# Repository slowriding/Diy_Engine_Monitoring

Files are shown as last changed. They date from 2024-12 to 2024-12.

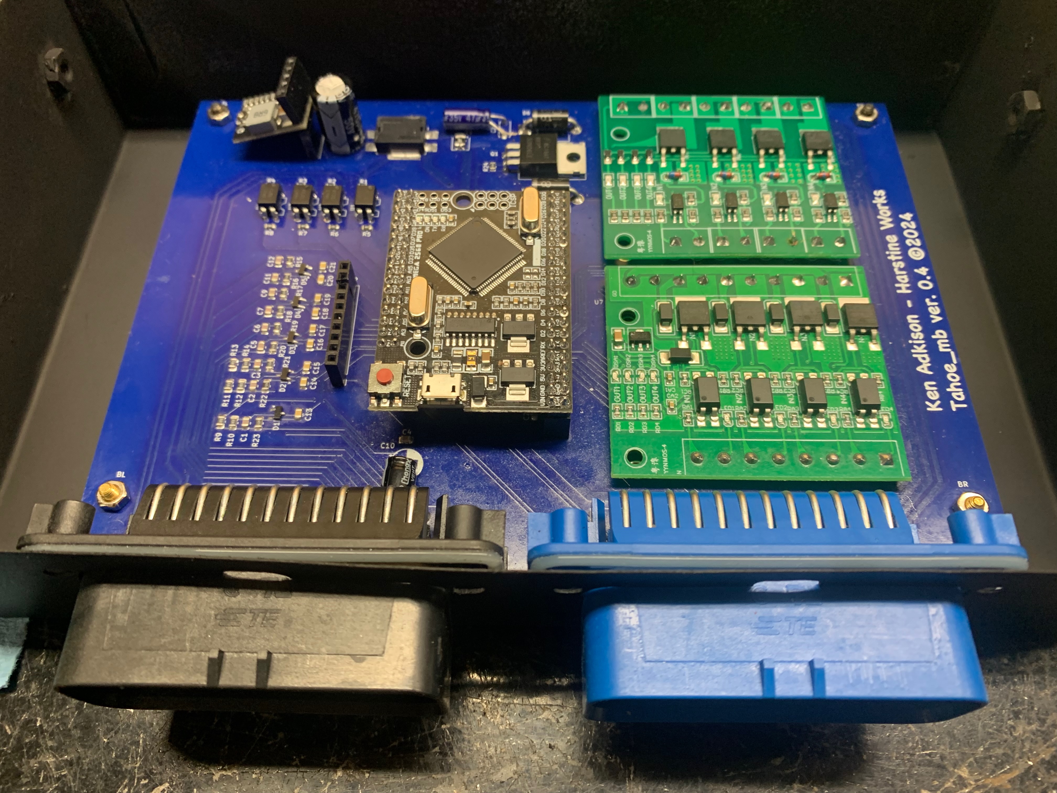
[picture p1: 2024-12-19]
PCB.jpeg

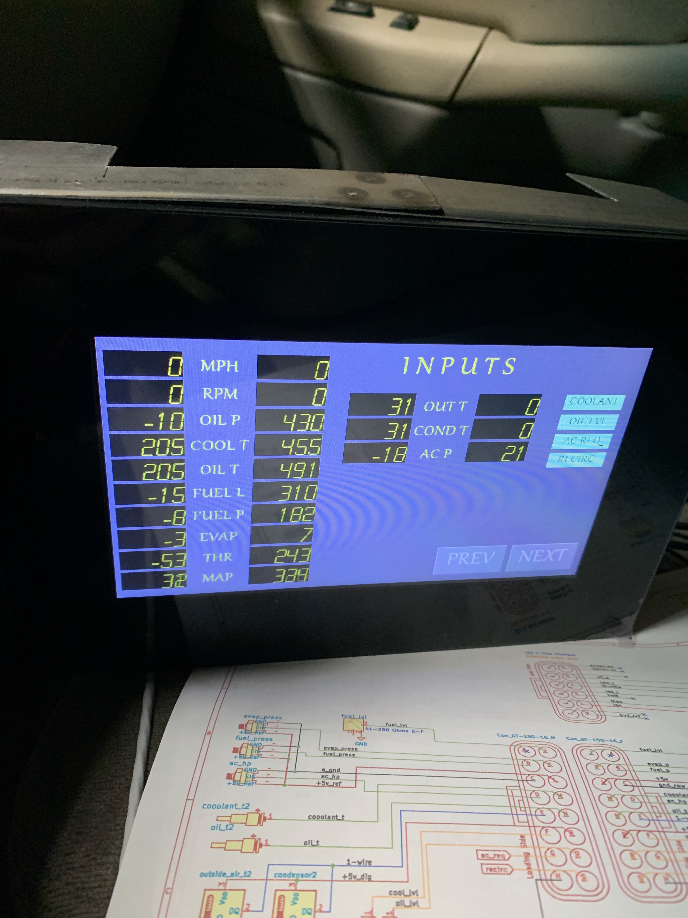
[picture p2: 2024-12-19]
Early_screenshot.jpeg

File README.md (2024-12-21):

# Diy_Engine_Monitoring
Read and display Powertrain sensors and control outputs with DIY PCB, code and display.

Project started to facilitate features lost due to swapping in newer engine into older computer controlled vehicle.
It overlays a secondary set of sensors and display unit showing gauges.
The controller drive outputs for variable speed loads like fans and fuel pump and switched loads.
Goals are for the system to be as simple as possible, hackable and start immediately without having to boot an operating system.

Project started to facilitate features lost due to swapping in newer engine into older computer controlled vehicle.
It overlays a secondary set of sensors and a display unit showing gauges.
The controller drives outputs for variable speed loads like fans and fuel pump and switched loads.
Goals are for the system to be as simple as possible, hackable and start immediately without having to boot an operating system.

Current design uses a common Arduino module programmed in C.  This project welcomes submissions of improvements or complete redesigns.
OBDII and GM LAN integration are intended but not completed.

Test article implementation:
2002 Chevrolet Tahoe with 5.3L gas engine failed and Chevrolet Performance E-ROD LS3 powertrain was installed with 6-speed manual transmission necessitating ECU swap.
The communications network is too different to interconnect directly.
The original dashboard gauges and A/C became completely non-functional due to the communications bus changes and features not implemented in newer but generic engine controller.

This project side steps difficulties in attempting to build a protocol converter; for the time being.
Requirements are met by adding a layer of sensors and outputs to replace missing features and adding some extra functionality.
I (original contributor) intend to hack my 2002 Tahoe dash to driving of stock gauge needles.
This will also control new style variable A/C compressor based on pressure and temperature sensors.

Design overview:
Sensors types:  // currently implemented but not all yet working.
	Resistive (coolant & oil temp and fuel level).
	0-5V transducers (oil, fuel, evap. and A/C high pressure)
	0-5V ECU outputs (throttle and map)
	Pulse frequency (RPM and vehicle speed ~10-14V)
	Switched (ac & recirculation requests)
	1-wire temperature probes (outside air and A/C condenser temperatures)

Outputs types:
	PWM Gauges Drivers (fuel level, oil pressure, coolant temperature, MPH)
	PWM Loads (fan1, fan2, Variable A/C compressor, Fuel Pump speed)

Interface:
	Display - Nextion brand Intelligent LCD display used due to it’s simple serial port/text based connection.
	All the graphics are stored and processed on the display.
	I2c & SPI connections for future ODB2 interfaces.

Programming:
	Currently written in C with migration to RUST intended for future releases.
	The Tahoe.h file isolates MCU pin definitions, calibrations and variable definitions.

Files:
	Schmatic: See .pdf files in root or Open directorys in KiCAD One is the PCB and the other shows the wiring currenly used on authors Tahoe

Code: Open Using Arduino software

Please consider contributing to this evolving project as much can be improved

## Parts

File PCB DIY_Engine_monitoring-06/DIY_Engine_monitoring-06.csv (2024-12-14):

Source: | /Users/kennethadkison/syncthing/tahoe/KiCAD/Tahoe_inputs_PCB-0_4/Tahoe_inputs_PCB-0_4.kicad_sch
Date: | Wednesday, December 06, 2023 at 08:47:50 AM
Tool: | Eeschema 7.0.9
Generator: | /Applications/KiCad/KiCad.app/Contents/SharedSupport/plugins/bom_csv_grouped_by_value_with_fp.py
Component Count: | 74
Ref | Qnty | Value | Cmp name | Footprint | Description | Vendor | DNP
C1, C2, C3, C4, C5, C6, C7, C8, C9, C10, C11, C12 | 12 | .1uf | C_Small | Capacitor_SMD:C_0805_2012Metric_Pad1.18x1.45mm_HandSolder | Unpolarized capacitor, small symbol
C13, C14 | 2 | 47uf_35v | C_Polarized_Small | Capacitor_THT:CP_Radial_D6.3mm_P2.50mm | Polarized capacitor, small symbol
C15, C16, C17, C18, C19, C20, C21, C22, C23, C24, C25, C26 | 12 | .22uf | C_Small | Capacitor_SMD:C_0805_2012Metric_Pad1.18x1.45mm_HandSolder | Unpolarized capacitor, small symbol
C27, C28, C29 | 3 | 100nf | C_Small | Capacitor_SMD:C_0805_2012Metric_Pad1.18x1.45mm_HandSolder | Unpolarized capacitor, small symbol
C30 | 1 | 1uf | C_Small | Capacitor_SMD:C_0805_2012Metric_Pad1.18x1.45mm_HandSolder | Unpolarized capacitor, small symbol
C31, C32 | 2 | 0.1uf | C_Small | Capacitor_SMD:C_0805_2012Metric_Pad1.18x1.45mm_HandSolder | Unpolarized capacitor, small symbol
D1, D2, D3, D4, D5, D6 | 6 | BZB84-B5V1,215 | BZB84-B5V1,215_2 | Package_TO_SOT_SMD:SOT-23-3 | 300mW Double Zener Diode, SOT-23
F1 | 1 | Polyfuse_0.5A | Polyfuse_Small | Diode_SMD:Littelfuse_PolyZen-LS | Resettable fuse, polymeric positive temperature coefficient, small symbol
FL1 | 1 | BNX025H01L | Filter_BNX025H01L | BNX025H01L:FIL_BNX025H01L
J1 | 1 | 5V_P/S | Conn_01x05 | Connector_PinHeader_2.54mm:PinHeader_1x05_P2.54mm_Vertical | Generic connector, single row, 01x05, script generated (kicad-library-utils/schlib/autogen/connector/)
J2 | 1 | Freematics-I2C | Conn_01x04 | Connector_PinHeader_2.54mm:PinHeader_1x04_P2.54mm_Vertical | Generic connector, single row, 01x04, script generated (kicad-library-utils/schlib/autogen/connector/)
J3 | 1 | Screw_Terminal_01x08 | Screw_Terminal_01x08 | Connector_Phoenix_MC_HighVoltage:PhoenixContact_MC_1,5_8-GF-5.08_1x08_P5.08mm_Horizontal_ThreadedFlange_MountHole | Generic screw terminal, single row, 01x08, script generated (kicad-library-utils/schlib/autogen/connector/)
J4, J5 | 2 | Conn_01x08 | Conn_01x08 | Connector_JST:JST_XH_B8B-XH-A_1x08_P2.50mm_Vertical | Generic connector, single row, 01x08, script generated (kicad-library-utils/schlib/autogen/connector/)
J6, J7 | 2 | test_acess | Conn_01x06 | Connector_PinHeader_2.54mm:PinHeader_1x06_P2.54mm_Vertical | Generic connector, single row, 01x06, script generated (kicad-library-utils/schlib/autogen/connector/)
J8 | 1 | 3.3v_P/S | Conn_01x05 | Connector_PinHeader_2.54mm:PinHeader_1x05_P2.54mm_Vertical | Generic connector, single row, 01x05, script generated (kicad-library-utils/schlib/autogen/connector/)
J9 | 1 | CANBus-Dual | Conn_02x09_Odd_Even | Connector_PinHeader_2.54mm:PinHeader_2x09_P2.54mm_Vertical | Generic connector, double row, 02x09, odd/even pin numbering scheme (row 1 odd numbers, row 2 even numbers), script generated (kicad-library-utils/schlib/autogen/connector/)
J10, J11 | 2 | Processor_01x10 | Conn_01x10 | Connector_JST:JST_XH_B10B-XH-A_1x10_P2.50mm_Vertical | Generic connector, single row, 01x10, script generated (kicad-library-utils/schlib/autogen/connector/)
R1, R2, R9, R10 | 4 | 2.49k | R_Small_US | Resistor_SMD:R_1206_3216Metric_Pad1.30x1.75mm_HandSolder | Resistor, small US symbol
R3 | 1 | 470 | R_Small_US | Resistor_SMD:R_1206_3216Metric_Pad1.30x1.75mm_HandSolder | Resistor, small US symbol
R4, R5, R6, R7, R8, R11, R12, R13, R14, R15, R16 | 11 | 470 | R_Small_US | Inductor_SMD:L_1206_3216Metric_Pad1.42x1.75mm_HandSolder | Resistor, small US symbol
R17, R18 | 2 | 10kΩ | R | Inductor_SMD:L_1206_3216Metric_Pad1.22x1.90mm_HandSolder | Resistor
SW1 | 1 | PWR_Source | SW_SPDT | Button_Switch_SMD:SW_SPDT_PCM12 | Switch, single pole double throw
U1, U2, U3 | 3 | ADS1115IDGS | ADS1115IDGS | Package_SO:TSSOP-10_3x3mm_P0.5mm | Ultra-Small, Low-Power, I2C-Compatible, 860-SPS, 16-Bit ADCs With Internal Reference, Oscillator, and Programmable Comparator, VSSOP-10
U4 | 1 | TXS0108EPW | TXS0108EPW | Package_SO:TSSOP-20_4.4x6.5mm_P0.65mm | Bidirectional level-shifting voltage translator, TSSOP-20

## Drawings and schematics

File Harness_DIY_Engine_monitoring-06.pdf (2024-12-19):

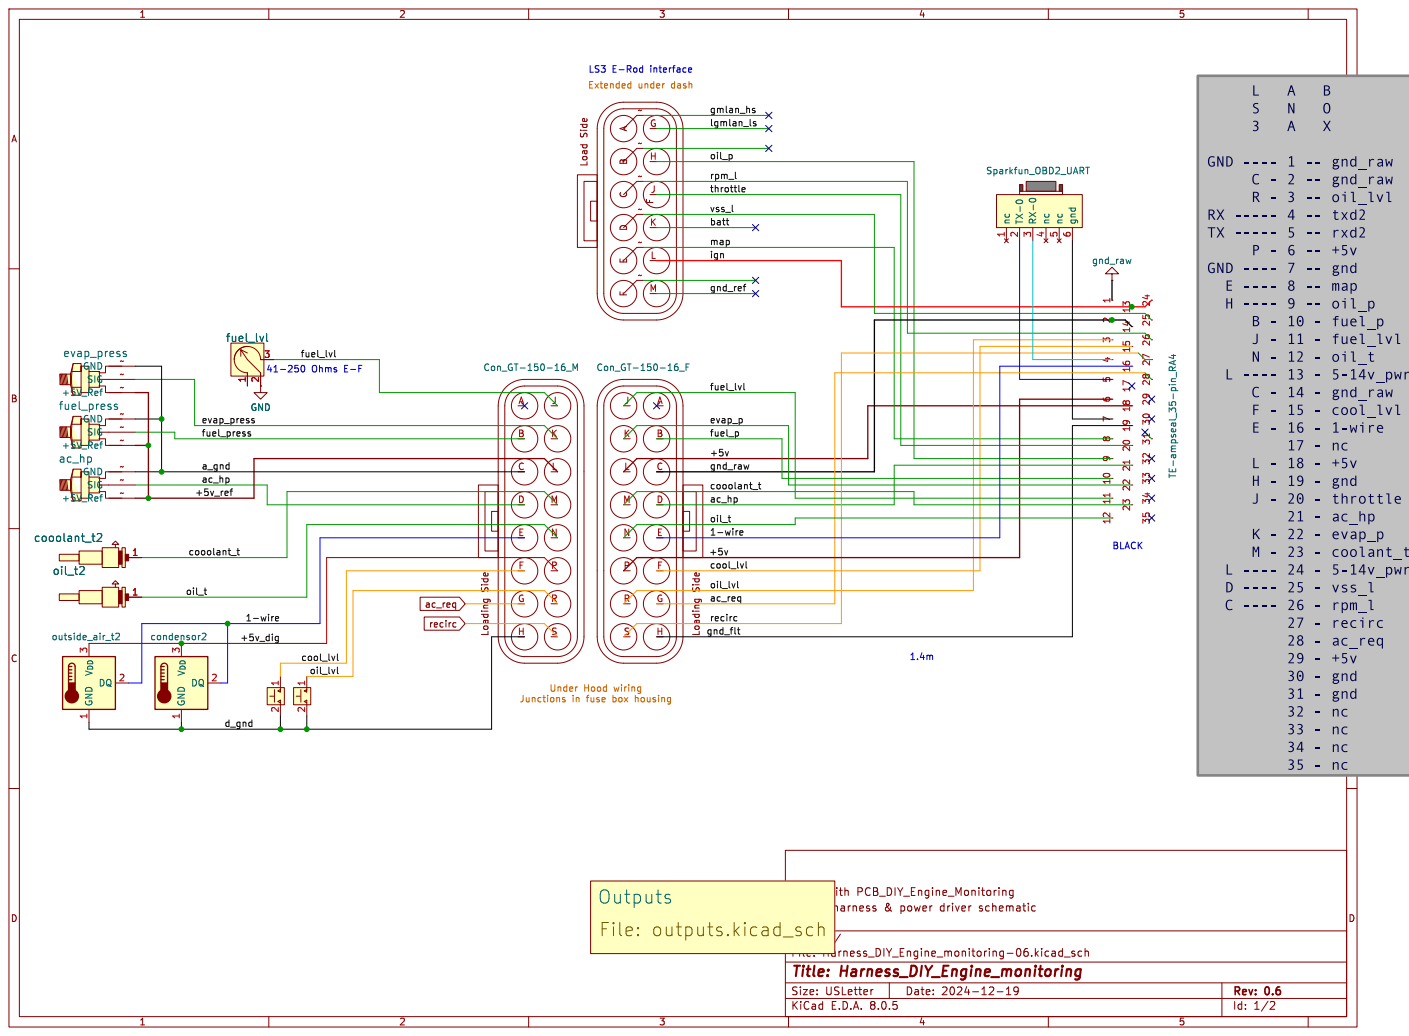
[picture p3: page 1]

1 2 http://docs.longan-labs.cc/1030019/ VIN

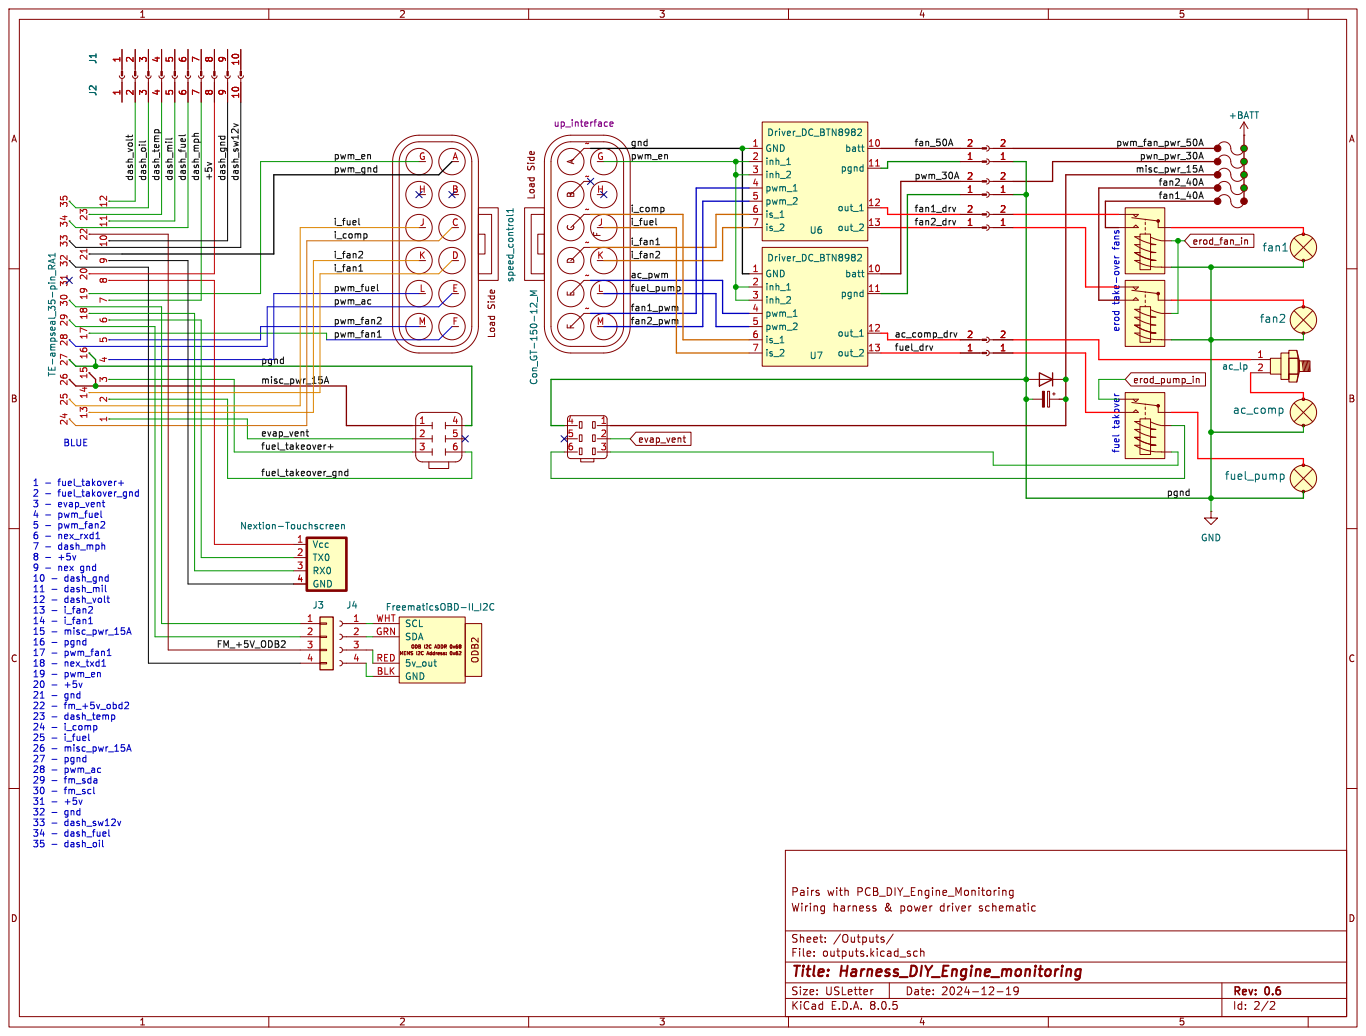
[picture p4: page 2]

+BATT
pwm_fan_pwr_50A erod take-over fans fuel takover

Wiring harness & | | PCB_DIY_Engine_Monitoring | power | driver schematic Pairs with

E.D.A. 8.0.5 Size: USLetter | Rev: 0.6 | | | | D Date: 2024-12-19 KiCad

File: outputs.kicad_sch Sheet: /Outputs/
Id: 2/2 Title: Harness_DIY_Engine_monitoring

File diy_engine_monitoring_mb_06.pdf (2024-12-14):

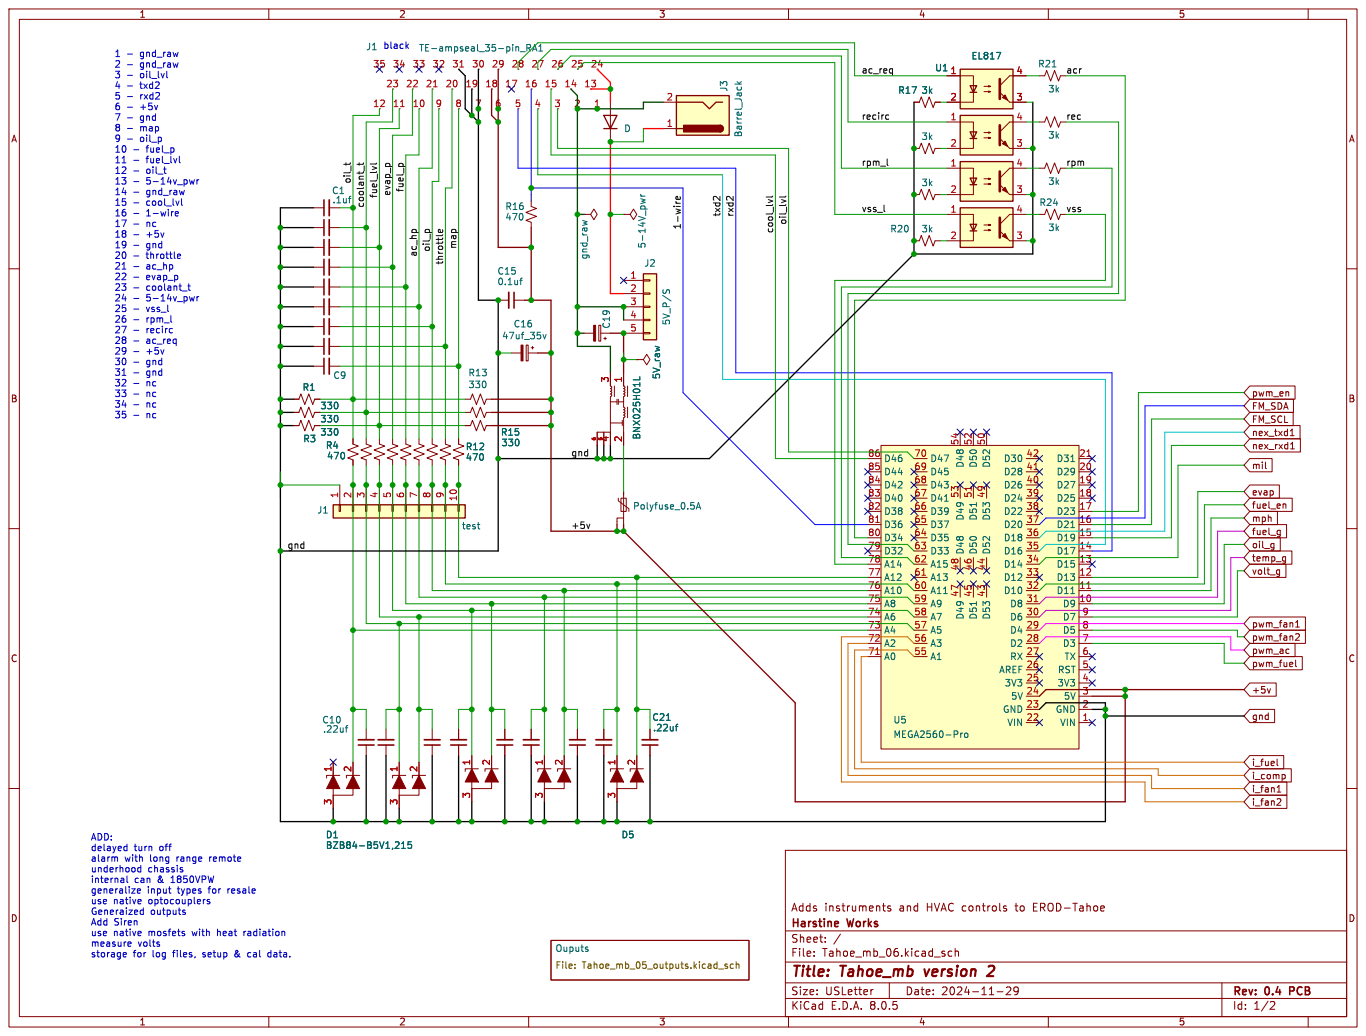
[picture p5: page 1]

storage for log files, setup & cal data. 1 - gnd_raw 2 - gnd_raw 3 - oil_lvl 4 - txd2 5 - rxd2 6 - +5v 7 - gnd 8 - map 9 - oil_p

31 - gnd

gnd +5v ADD: delayed turn off alarm with long range remote

use native optocouplers Generaized outputs Add Siren

use native mosfets with heat radiation measure volts

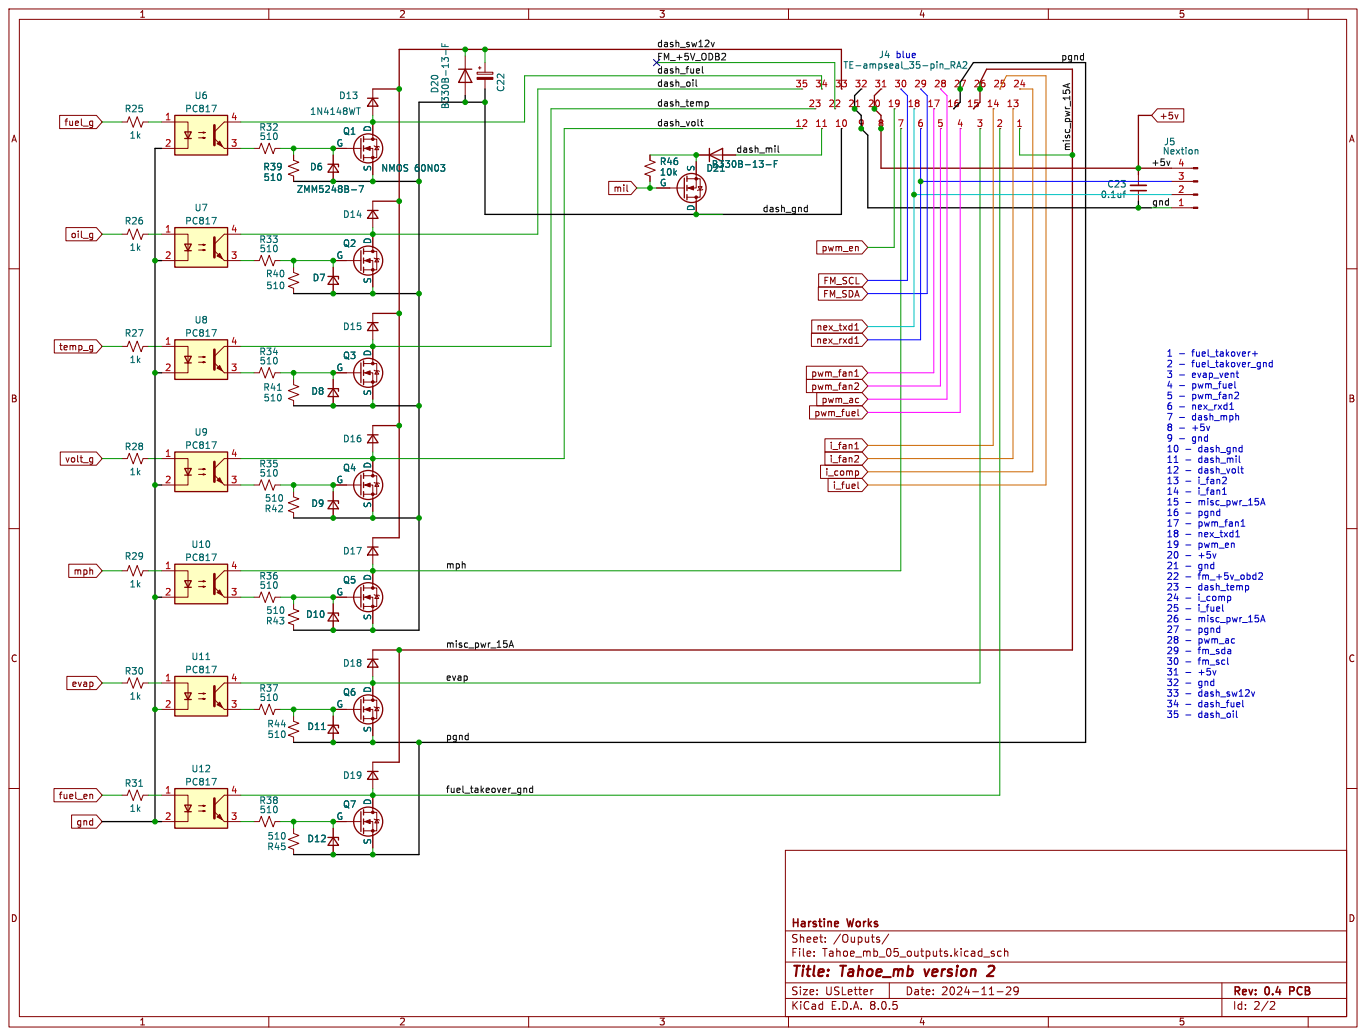
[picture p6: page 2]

File: Tahoe_mb_05_outputs.kicad_sch Sheet: /Ouputs/ Harstine Works

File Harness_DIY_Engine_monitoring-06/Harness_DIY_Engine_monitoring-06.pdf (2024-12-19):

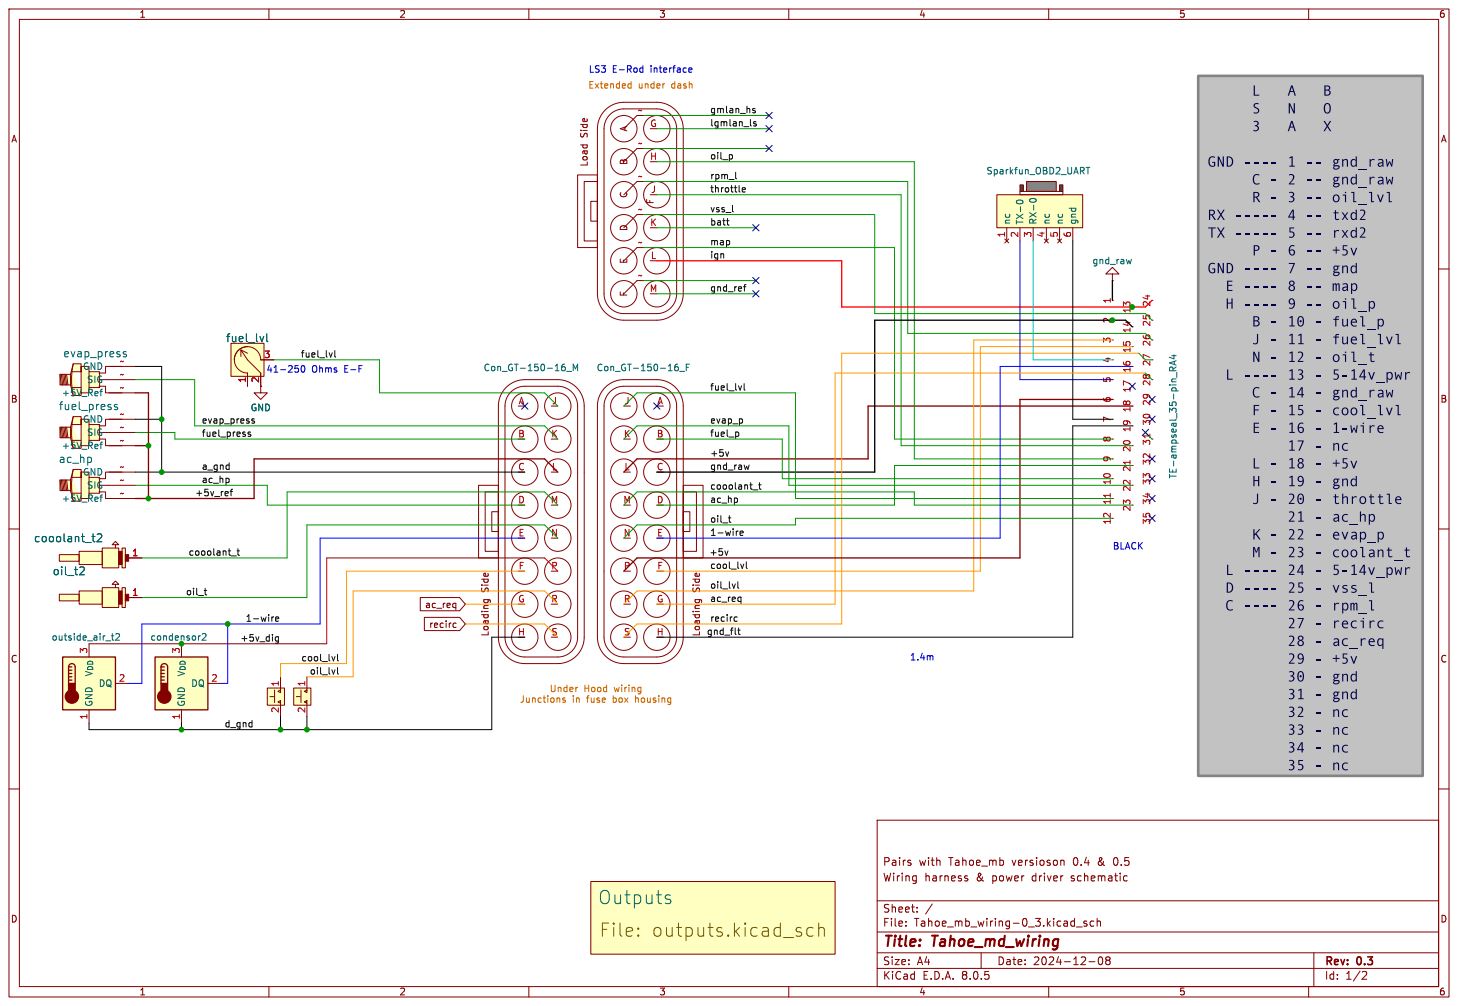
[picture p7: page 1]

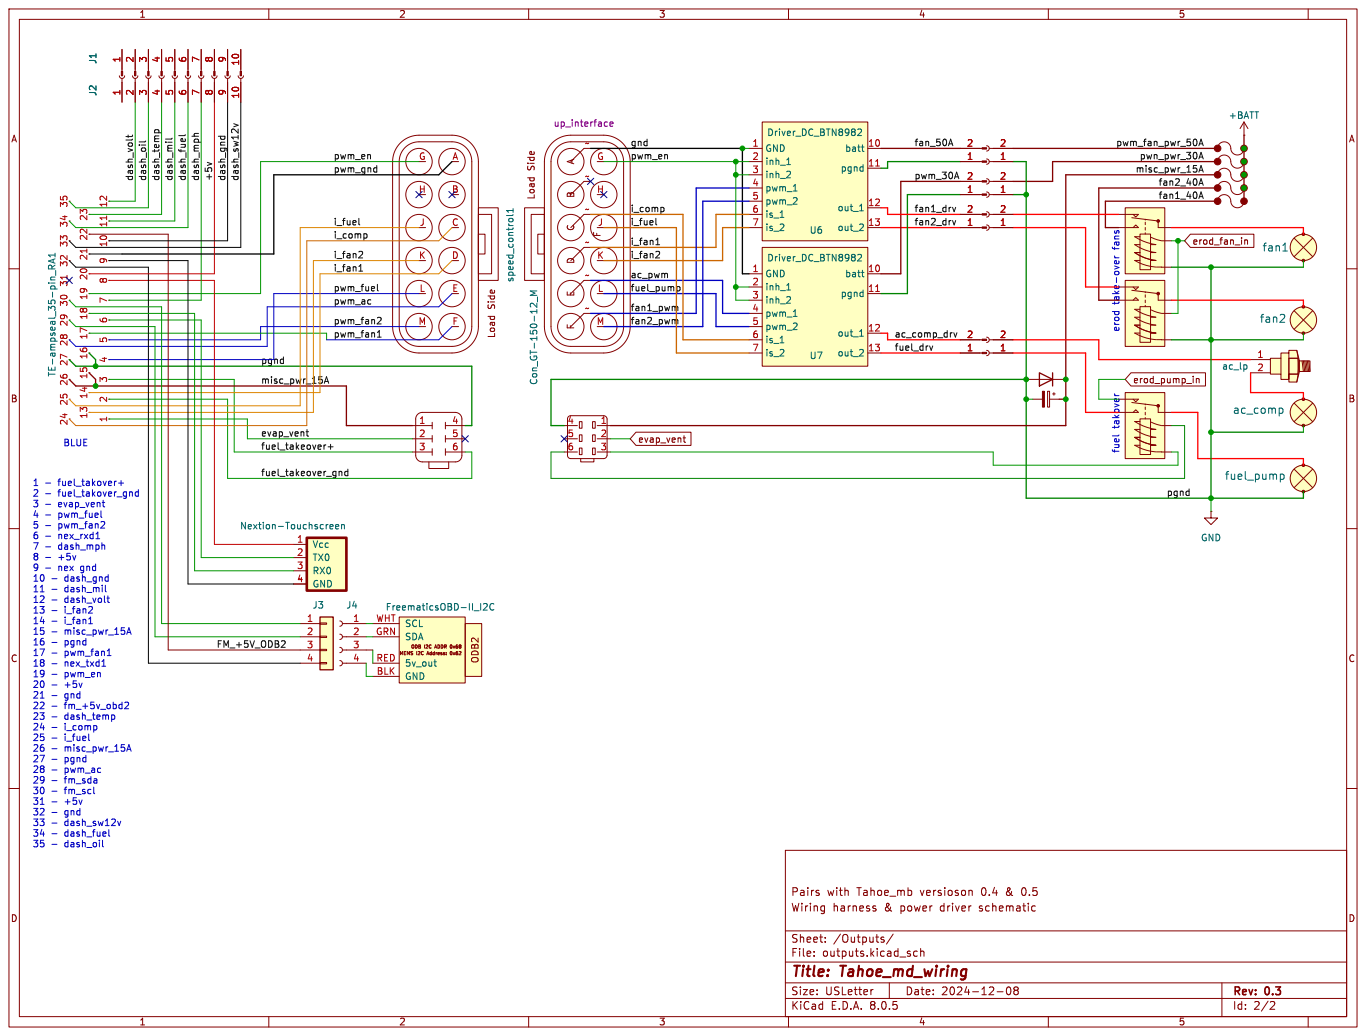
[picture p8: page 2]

pwm_fan_pwr_50A erod take-over fans fuel takover 1 - fuel_takover+ 2 - fuel_takover_gnd 3 - evap_vent 4 - pwm_fuel 5 - pwm_fan2 6 - nex_rxd1 7 - dash_mph 8 - +5v 9 - nex gnd

File: outputs.kicad_sch Sheet: /Outputs/
Id: 2/2 Title: Tahoe_md_wiring

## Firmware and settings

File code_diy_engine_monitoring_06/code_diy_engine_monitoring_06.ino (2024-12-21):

/*************************************************************************
  * DIY_Engine_Monitoring and controls
  * Originally developed for: Chevrolet Performance EROD-LS3 6.2L powertrian to 2002 Tahoe chassis interface
  *
  * Written by Ken Adkison
  * From examples and libraries by the following:
  *
  * Revison History
  *
  * Renamed and pushed to GitHub now DIY_engine_monitoring_06 - Dec 14, 2024 
  * tahoe_mb_b_0_4.ino - pins reumbered
  * Major Revision - Revised PCB - All 5V Mega2560 based
  * tahoe_nex_07.ino - abandaning CAN - adding fan and AC speed controllers
  * taheo_nex_06_seeed.ino test version for seeed_can using MOSI
  * taheo_nex_06.ino - changed back to freematics
  * taheo_nex_05.ino - A/D works and displays on nextion, partly functional, no CAN
  * tahoe_nex_04.ino - Added previous looping structure to OBD2 PID data processsing 
  * tahoe_nex_03.ino 4/2/2024 - Restructured to loop through structures of A/D readings, calibrations, and display objects.  
  *   Reused loops shortens code providing a better structure for expanded desplay functionality later.
  * tahoe_nex_02.ino - First version with working Nextion display working from A/D data
  *
  /*************************************************************************************************
      OBD-II_PIDs TEST CODE
      LOOVEE @ JUN24, 2017

      Query
      send id: 0x7df
        dta: 0x02, 0x01, PID_CODE, 0, 0, 0, 0, 0

      Response
      From id: 0x7E9 or 0x7EA or 0x7EB
        dta: len, 0x41, PID_CODE, byte0, byte1(option), byte2(option), byte3(option), byte4(option)

      https://en.wikipedia.org/wiki/OBD-II_PIDs

      Input a PID, then you will get reponse from vehicle, the input should be end with '\n'
  ***************************************************************************************************/

  #include <Arduino.h>
  // #include <Wire.h> // Master is MEGA 2560
  #include <DS18B20.h>

  //#include "nextion_disp.h"  Not required at this time

  #include "tahoe.h"  // definitions and calibrations

  #define DS18B20          // 1-wire temp sensors
  // #define DEBUG1        // AD RAW & limiter display - Comment this out if you don't need to see what happens in the serial Monitor
  // #define DEBUG2        // Nextion display command feed - Comment this out if you don't need to see
  // #define DEBUG3        // Mapped values - Comment this out if you don't need to see what happens in the serial Monitor
  // #define FAKE          // Faking data for bench testing without sensors
  // #define OUTPUT_TEST   // Driver outputs exercised for testing
  #define WIRE
  #define TRACER

  #ifdef TRACER
    #include <ArduinoTrace.h>
  #endif

void sendCmd(String cmd)
  {
    nexSer.print(cmd);
    nexSer.write("\xFF\xFF\xFF");
    #ifdef DEBUG2
      if(cmd.length() > 0)
      {
        dbgSer.print("Sending command : ");
        dbgSer.println(cmd);
      } else
      {
        dbgSer.println("Empty command issued to clear the buffer"); 
      }
    #endif  
  }


void output_test()
  {
    while(1) {
      dbgSer.println("output.test");
      int i;
      for(i=75; i<=254; i++) {
        analogWrite(fan1_pin, i);
        sendCmd(nexOut[0].text + String(i));
        ad_in(I_FAN1, analogRead(i_fan1));
        delay(50);
      }
      analogWrite(fan1_pin, 0);
      sendCmd(nexOut[0].text + String(0));
      delay(250);

      for(i=75; i<=254; i++) {
        analogWrite(fan2_pin, i);
        sendCmd(nexOut[1].text + String(i));
        ad_in(I_FAN2, analogRead(i_fan2));
        delay(50);
      }
      analogWrite(fan2_pin, 0);
      sendCmd(nexOut[1].text + String(0));
      delay(250);

      analogWrite(fan1_pin, 254);
      sendCmd(nexOut[0].text + String(254));
      delay(2000);
      ad_in(I_FAN1, analogRead(i_fan1));
      analogWrite(fan1_pin, 0);
      sendCmd(nexOut[0].text + String(0));
      delay(500);
      ad_in(I_FAN1, analogRead(i_fan1));
      analogWrite(fan2_pin, 254);
      sendCmd(nexOut[1].text + String(254));
      delay(2000);
      ad_in(I_FAN2, analogRead(i_fan2));
      analogWrite(fan2_pin, 0);
      sendCmd(nexOut[1].text + String(0));
      delay(500);
      ad_in(I_FAN2, analogRead(i_fan2));

      for(i=0; i<=254; i++) {
        analogWrite(pwm_ac_pin, i);
        sendCmd(nexOut[2].text + String(i));
        delay(50);
        ad_in(I_COMP, analogRead(I_COMP));
      }
      analogWrite(pwm_ac_pin, 0);
      sendCmd(nexOut[2].text + String(0));
      for(i=0; i<=3; i++) {
        analogWrite(pwm_ac_pin, 254);
        sendCmd(nexOut[2].text + String(254));
        delay(250);
        ad_in(I_COMP, analogRead(I_COMP));
        analogWrite(pwm_ac_pin, 0);
        sendCmd(nexOut[2].text + String(0));
        delay(250);
        ad_in(I_COMP, analogRead(I_COMP));
      }


      for(i=0; i<=3; i++) {
        digitalWrite(evap_pin, 1);
          sendCmd(nexOut[10].bco + String(50712));
          sendCmd(nexOut[10].pco + String(0));
          delay(250);
        digitalWrite(evap_pin, 0);
          sendCmd(nexOut[10].bco + String(12678));
          sendCmd(nexOut[10].pco + String(65504));
          delay(250);
      }

      digitalWrite(fuel_en_pin, 1);
        sendCmd(nexOut[9].bco + String(50712));
        sendCmd(nexOut[9].pco + String(0));

      for(i=0; i<=254; i++) {
        analogWrite(pwm_fuel_pin, i);
        sendCmd(nexOut[3].text + String(i));
        delay(50);
        ad_in(I_FUEL, analogRead(i_fuel));
      }
      analogWrite(pwm_fuel_pin, 0);
        digitalWrite(fuel_en_pin, 0);
        sendCmd(nexOut[3].text + String(0));
        sendCmd(nexOut[9].bco + String(12678));
        sendCmd(nexOut[9].pco + String(65504));
        ad_in(I_FUEL, analogRead(i_fuel));

      for(i=0; i<=5; i++) {
        analogWrite(mil_pin, 254);
        sendCmd(nexOut[11].bco + String(63488));
        
        DUMP(nexOut[11].bco + String(63488));
        Serial.println(nexOut[11].bco + String(63488));

        delay(500);
        analogWrite(mil_pin, 0);
        sendCmd(nexOut[11].bco + String(12678));
        delay(150);
      }


      for(i=0; i<=254; i++) {
        analogWrite(mphg_pin, i);
        sendCmd(nexOut[4].text + String(i));
        delay(25);
      }
      analogWrite(mphg_pin, 0);
      sendCmd(nexOut[4].text + String(0));

      for(i=0; i<=254; i++) {
        analogWrite(fuelg_pin, i);
        sendCmd(nexOut[5].text + String(i));
        delay(25);
      }
      analogWrite(fuelg_pin, 0);
      sendCmd(nexOut[5].text + String(0));

      for(i=0; i<=254; i++) {
        analogWrite(oilg_pin, i);
        sendCmd(nexOut[6].text + String(i));
        delay(25);
      }
      analogWrite(oilg_pin, 0);
      sendCmd(nexOut[6].text + String(0));

      for(i=0; i<=254; i++) {
        analogWrite(tempg_pin, i);
        sendCmd(nexOut[7].text + String(i));
        delay(25);
      }
      analogWrite(tempg_pin, 0);
      sendCmd(nexOut[7].text + String(0));

      for(i=0; i<=254; i++) {
        analogWrite(voltg_pin, i);
        sendCmd(nexOut[8].text + String(i));
        delay(25);
      }
      analogWrite(voltg_pin, 0);
      sendCmd(nexOut[8].text + String(0));
    }
  }


void ad_in(uint16_t ad, uint16_t raw)  // Process A/D input
  {
    if(millis() >= timeTarget[ad]) {    // if timer has progressed pasted target
      timeTarget[ad] = millis() + refresh[ad];  // add the refresh delay to the timer to reduce cpu load
      // DUMP(curr_val[ad]);
      
      /*if(cal[ad].rawLo < cal[ad].rawHi)  {  // Normal
        if(raw < cal[ad].rawLo)  raw = cal[ad].rawLo;    // safety if all else fails !! Should set error
        if(raw > cal[ad].rawHi)  raw = cal[ad].rawHi;    // safety if all else fails
      } else if(cal[ad].rawLo > cal[ad].rawHi)  {  // Low and Ho can be reversed in some calibrations
        if(raw > cal[ad].rawLo)  raw = cal[ad].rawLo;    // safety if all else fails !! Should set error
        if(raw < cal[ad].rawHi)  raw = cal[ad].rawHi;    // safety if all else fails 
      }
      */
      //DUMP(ad);
      //DUMP(raw);
      curr_val[ad] = map(raw, cal[ad].rawLo, cal[ad].rawHi, cal[ad].calLo, cal[ad].calHi);   // apply calibrations to A/D inputs
      //DUMP(curr_val[ad]);

      //if(curr_val[ad] != last_val[ad]) {    // if the results have not changed from the last value, don't bother updating

        if(damping[ad] != 0) {    // dampen fuel gauge from displaying slosh   *********** test **********
          curr_val[ad] = (unsigned long)((last_val[ad] * damping[ad]) + (curr_val[ad] * (1 - damping[ad])));  // New value updates old value at most by 20%
          // DUMP(curr_val[6]);
        }

        if(curr_val[ad] >= gauge[ad].warn_l && curr_val[ad] <= gauge[ad].warn_h) sendCmd(nexObj[ad].pco + String(26508)); // gauge in normal value display GREEN
        else if(curr_val[ad] >= gauge[ad].crit_l && curr_val[ad] <= gauge[ad].warn_l) sendCmd(nexObj[ad].pco + String(65504)); // Warning low YELLOW
        else if(curr_val[ad] >= gauge[ad].warn_h && curr_val[ad] <= gauge[ad].crit_h) sendCmd(nexObj[ad].pco + String(65504)); // warning high YELLOW
        else if(curr_val[ad] <= gauge[ad].crit_l || curr_val[ad] >= gauge[ad].crit_h) sendCmd(nexObj[ad].pco + String(63488)); // critical alarm RED
        else sendCmd(nexObj[ad].pco + String(63488));
        
        sendCmd(nexObj[ad].raw + String(raw));
        // TRACE();
        sendCmd(nexObj[ad].text + String(curr_val[ad]));  // update text readout
        sendCmd(nexObj[ad].gauge + String(map(curr_val[ad], gauge[ad].start, gauge[ad].stop, 0, 100)));  // update bar graph
        
        last_val[ad] = curr_val[ad];
      //}
    }
  }
  

void setup() {
  // dbgSer.setDebugOutput(false);  // see Wire master
  // Wire.setSDA(0);
  // Wire.setSCL(1);

  // Wire.begin();
  //   delay(100);  // Wire settling ?

  dbgSer.begin(38400);  // debug
  while(!dbgSer);
  nexSer.begin(38400);  // Nextion display feed - Some dropout with long cable at 115200
  while(!nexSer);
  sendCmd(""); // clear the buffer

  //  INPUTS
  pinMode(ac_req_pin, INPUT_PULLUP);
  pinMode(ac_recirc_pin, INPUT_PULLUP);
  pinMode(oil_lvl_pin, INPUT_PULLUP);
  pinMode(cool_lvl_pin, INPUT_PULLUP);

  pinMode(rpm_pin, INPUT_PULLUP);
  pinMode(vss_pin, INPUT_PULLUP);

  // OUTPUTS
  pinMode(pwm_ac_pin, OUTPUT);
  pinMode(pwm_fuel_pin, OUTPUT);
  pinMode(fan1_pin, OUTPUT);
  pinMode(fan2_pin, OUTPUT);
  pinMode(pwm_en_pin, OUTPUT);

  pinMode(tempg_pin, OUTPUT);
  pinMode(voltg_pin, OUTPUT);
  pinMode(fuelg_pin, OUTPUT);
  pinMode(oilg_pin, OUTPUT);
  pinMode(mphg_pin, OUTPUT);
  pinMode(mil_pin, OUTPUT);

  pinMode(fuel_en_pin, OUTPUT);
  pinMode(evap_pin, OUTPUT);


  for(i=0; i<=24; i++)  // send zeros to all display objects  *** KEEP UP TO DATE
    {
    sendCmd(nexObj[i].raw + String(0));
    sendCmd(nexObj[i].text + String(0));
    }

  #ifdef FAKE
    fake_raw[OIL_P]  = cal[OIL_P].rawLo;
    fake_raw[COOL_T] = cal[COOL_T].rawLo;
    fake_raw[OIL_T]  = cal[OIL_T].rawLo;
    fake_raw[FUEL_L] = cal[FUEL_L].rawLo;
    fake_raw[FUEL_P] = cal[FUEL_P].rawLo;
    fake_raw[EVAP]   = cal[EVAP].rawLo;
    fake_raw[AC_HP]  = cal[AC_HP].rawLo;
    fake_raw[THR]    = cal[THR].rawLo;
    fake_raw[MAP]    = cal[MAP].rawLo;
  #endif  // FAKE

  // digitalWrite(pwm_en_pin,  1);

  #ifdef DS18B20
    dbgSer.print("1-wire Devices: ");
    dbgSer.println(ds.getNumberOfDevices());
      while (ds.selectNext()) {
      switch (ds.getFamilyCode()) {
        case MODEL_DS18S20:
          dbgSer.println("Model: DS18S20/DS1820");
          break;
        case MODEL_DS1822:
          dbgSer.println("Model: DS1822");
          break;
        case MODEL_DS18B20:
          dbgSer.println("Model: DS18B20");
          break;
        default:
          dbgSer.println("Unrecognized Device");
          break;
      }

      uint8_t address[8];
      ds.getAddress(address);

      dbgSer.print("Address:");
      for (uint8_t i = 0; i < 8; i++) {
        dbgSer.print(" ");
        dbgSer.print(address[i]);
      }
      dbgSer.println();

      dbgSer.print("Resolution: ");
      dbgSer.println(ds.getResolution());

      dbgSer.print("Power Mode: ");
      if (ds.getPowerMode()) {
        dbgSer.println("External");
      } else {
        dbgSer.println("Parasite");
      }

      dbgSer.print("Temperature: ");
      dbgSer.print(ds.getTempC());
      dbgSer.print(" C / ");
      dbgSer.print(ds.getTempF());
      dbgSer.println(" F");
      dbgSer.println();
    }
  #endif  // DS18B20 WIRE
  

  #ifdef OUTPUT_TEST
   output_test();
  #endif
}  //  End Setup


void loop() {  // MAIN LOOP ******************************************************
  // rpm = pulseIn(rpm_pin, HIGH);  //  rpm = 1 / pulseIn(rpm_pin, HIGH);  VERY SLOW
  // vss = pulseIn(vss_pin, HIGH);  //  vss = ((1 / pulseIn(vss_pin, HIGH)) / 60) / 800;  // pulses per mile is some standaard number 800?

  //  we have all values
  #ifdef DEBUG1 
    dbgSer.print("rpm = ");
    dbgSer.print(rpm);
    dbgSer.print(" , vss = ");
    dbgSer.println(vss);
  #endif

  #ifdef FAKE
      ad_in(OIL_P,  fake_raw[OIL_P]);
      dbgSer.println(nexObj[OIL_P].text + String(curr_val[OIL_P]));
      ad_in(COOL_T, fake_raw[COOL_T]);
      dbgSer.println(nexObj[COOL_T].text + String(curr_val[COOL_T]));
      ad_in(OIL_T,  fake_raw[OIL_T]);
      ad_in(FUEL_L, fake_raw[FUEL_L]);
      ad_in(FUEL_P, fake_raw[FUEL_P]);
      ad_in(EVAP,   fake_raw[EVAP]);
      ad_in(AC_HP,  fake_raw[AC_HP]);
      ad_in(THR,    fake_raw[THR]);
      ad_in(MAP,    fake_raw[MAP]);

      fake_raw[OIL_P] = fake_raw[OIL_P] +5;
      fake_raw[COOL_T] = fake_raw[COOL_T] -5;
      fake_raw[OIL_T] = fake_raw[OIL_T] -5;
      fake_raw[FUEL_L] = fake_raw[FUEL_L] +5;
      fake_raw[FUEL_P] = fake_raw[FUEL_P] +5;
      fake_raw[EVAP] = fake_raw[EVAP] +5;
      fake_raw[AC_HP] = fake_raw[AC_HP] +5;
      fake_raw[THR] = fake_raw[THR] +5;
      fake_raw[MAP] = fake_raw[MAP] +5;
  #endif  // FAKE data
  
    ad_in(OIL_P,  analogRead(oil_p_pin));
    ad_in(COOL_T, analogRead(cool_t_pin));
    ad_in(OIL_T,  analogRead(oil_t_pin));
    ad_in(FUEL_L, analogRead(fuel_l_pin));
    ad_in(FUEL_P, analogRead(fuel_p_pin));
    ad_in(EVAP,   analogRead(evap_pin));
    ad_in(AC_HP,  analogRead(ac_hp_pin));
  
    ad_in(I_FUEL, analogRead(i_fuel));
    ad_in(I_COMP, analogRead(i_comp));
    ad_in(I_FAN1, analogRead(i_fan1));
    ad_in(I_FAN2, analogRead(i_fan2));

    //ad_in(THR,    analogRead(thr_pin));
    //ad_in(MAP,    analogRead(map_pin))
  
  if(digitalRead(oil_lvl_pin) == 0) sendCmd("oilLvl.bco=" + String(63488));  // low oil
  else sendCmd("oilLvl.bco=" + String(26508));   // has oil

  if(digitalRead(cool_lvl_pin) == 1) sendCmd("coolLvl.bco=" + String(63488));  // low coolant
  else sendCmd("coolLvl.bco=" + String(26508));  
  
  if(nexSer.available() > 0)  // read data strings from Nextion Display
  {
    char Received = dbgSer.read();
    if (Received =='s')  {  // slider 1
      int num = nexSer.parseInt();
    }
  }

  ds.select(0);

  sendCmd(nexObj[15].text + String(int(ds.getTempF())));
  // ds.selectNext();
  ds.select(1);
  sendCmd(nexObj[16].text + String(int(ds.getTempF())));
  //   ds.selectNext();


  #ifdef WIRE
    dbgSer.print("1-wire Devices: ");
    dbgSer.println(ds.getNumberOfDevices());
    air_temp = ds.getTempC();
  #endif  // WIRE

  if(curr_val[COOL_T] < 170)  {  // engine_t
    fan1 = 0;
    fan2 = 0;
  }
  else if(curr_val[COOL_T] > 225)  {
    fan1 = 254;
    fan2 = 254;
  }
  else  {
    fan1 = map(curr_val[COOL_T], 180, 220, 80, 254);
    fan2 = map(curr_val[COOL_T], 180, 220, 80, 254);
  }
  /*
  #ifdef DEBUG3
    // a/c CVC compressor - Deslug startup by starting with no flow then adding inital flow slowly to get oil and liquid moving prior to adding flow
    dbgSer.print("ac_req= ");
    dbgSer.print(digitalRead(ac_req_pin));  // 1 = key off, key on ac off = 0, ac on = 0, fan off = 1, fan on = 0

    dbgSer.print(", ac_recirc= ");
    dbgSer.println(digitalRead(ac_recirc_pin));  // 1 = key off, key on & ac off = 0, ac & recirc = 1
  #endif

  if(digitalRead(ac_req_pin) = 0)  {
    if(fan1 < 150) { 
      fan1 = 150;
    }
    if(fan2 < 150) { 
      fan2 = 150;
    }
    if(curr_val[5] < 250)  {  // cool_t
      if (ac_comp < 50) {
        ac_comp = 50;
        analogWrite(pwm_ac_pin, ac_comp);
        delay(200);
      }
      else analogWrite(pwm_ac_pin, ac_comp);
    }
    sendCmd(nexOut[2].text + String(ac_comp));
  }
  */

  analogWrite(fan1_pin, fan1);
  analogWrite(fan2_pin, fan2);

  // The following seems like a safety - redundant
  if(curr_val[COOL_T] > 200)  {  // engine_t
    fan1 = 254;
    fan2 = 254;
    analogWrite(fan1_pin, fan1);
    analogWrite(fan2_pin, fan2);
  }
  sendCmd(nexOut[0].text + String(fan1));
  sendCmd(nexOut[1].text + String(fan2));
  */
}  // loop

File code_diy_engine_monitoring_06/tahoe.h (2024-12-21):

#include "pins_arduino.h"
#include <Arduino.h>
// #include <Wire.h> // Master is MEGA 2560

#define nexSer Serial1 // Controlling the Nextion HMI using serial1 (pin18 of the Arduino Mega) to prevent interfering with code upload
#define dbgSer Serial // Debug using default serial over USB towards Arduino serial Monitor


// int idx = 0;
// uint32_t last = 0, now = 0;  // for speed test
uint32_t i = 0;   // wire buffer

// int fake=0;    // fake data sequencer
// Variables used in logic control

// OBD2 decoded data from Freematics
uint16_t volts;
uint16_t load;
uint16_t manfp;
uint16_t engine_temp;
uint16_t rpm;
uint16_t vss;
uint16_t adv;
uint16_t air_temp;
uint16_t thr_pos;
uint16_t evap_press;

// ANALOG INPUTS              // Nextion fields
const int i_fuel       = A0;  // n73
const int i_comp       = A1;  // n72
const int i_fan1       = A2;  // n70
const int i_fan2       = A3;  // n71
const int oil_t_pin    = A4;  // n5:x5
const int cool_t_pin   = A5;  // n3:x3
const int fuel_l_pin   = A6;  // n4:x4
const int evap_pin     = A7;  // n7:x7
const int fuel_p_pin   = A8;  // n6:x6
const int ac_hp_pin    = A9;   // n10:x10
const int oil_p_pin    = A10;  // n2:x2
const int thr_pin      = A11;  // n8:x8
const int map_pin      = A12;  // n9:x9
const int vss_pin      = A14;  // n0:raw x0:mph
const int rpm_pin      = A15;  // n1:raw x1:rpm

const int ad_pins[] = {A0, A1, A2, A3, A4, A5, A6, A7, A8, A9, A10, A11, A12, A13, A14, A15};

// DIGITAL INPUTS
const int ac_req_pin   = 34;
const int ac_recirc_pin= 33;
const int oil_lvl_pin  = 28;
const int cool_lvl_pin = 32;

DS18B20 ds(36);  // reworked fix to PCB

// OUTPUTS
const int pwm_ac_pin   = 2;
const int pwm_fuel_pin = 3;
const int fan1_pin     = 4;
const int fan2_pin     = 5;

const int tempg_pin    = 6;
const int voltg_pin    = 7;
const int fuelg_pin    = 8;
const int oilg_pin     = 9;
const int fuel_en_pin  = 10;
const int mphg_pin     = 11;
const int evap_sol_pin = 13;  
const int mil_pin      = 14;
const int pwm_en_pin   = 23;

// Global variables
// static char buff[100]; // for CAN msgs via wire  //  ??? not used
bool ac_req   = false;
bool cool_lvl = false;
bool oil_lvl  = false;
bool fuel_en  = false;
bool evap     = false;


uint8_t rpm_l    = 0;
uint8_t mph_l    = 0;
uint8_t fan1     = 0;
uint8_t fan2     = 0;
uint8_t ac_pwm   = 0;
uint8_t fuel_pwm = 0;
uint8_t mil      = 255;
uint8_t voltg    = 0;
uint8_t oilg     = 0;
uint8_t tempg    = 0;
uint8_t fuelg    = 0;


float airTemp       = 0;
float condenserTemp = 0;

uint32_t timTarget = 0;
uint16_t interval  = 200;
uint32_t readVal   = 0;
int32_t  dispVal   = 0;
int32_t  lastVal   = 0;
int      ac_comp   = 0;

/*
// ----- OBD
#define map_calrawLo 0
#define map_calrawHi 65,535
#define map_calvalLo 0
#define map_calvalHi 255
*/

#define ac_fan_on_cond_t 185
#define ac_fan_off_vcc 35
#define ac_fan_on_vcc 35
#define ac_delay 1         // secs
#define ac_min_on_time 50  // secs
#define ac_p_en 219.9      // f
#define ac_p_dis 180.1     // f

#define fan_low_sp = 30
#define fan_hi_sp = 100

#define fan_coolant_low 185
#define fan_coolant_high 210
#define fan_sp_lo 75
#define fan_sp_hi 255
#define fan_delay 2000

#define ac_dis_rpm 4700
#define ac_en_rpm  4500
#define ac_dis_tps 90
#define ac_en_tps  30

#define I_FUEL 0   // Index to arrays
#define I_COMP 1
#define I_FAN1 2
#define I_FAN2 3

#define OIL_T  4
#define COOL_T 5
#define FUEL_L 6

#define EVAP   7
#define FUEL_P 8
#define AC_HP  9
#define OIL_P  10
#define THR    11
#define MAP    12

#define MPG    13
#define RPM    14
#define AIRT   15
#define ACT    16


struct calVal {
  uint16_t rawLo;   // lowest A/D RAW sensor reading
  uint16_t rawHi;   // highest A/D RAW sensor reading
  uint16_t calLo;   // lowest gauge displayed value
  uint16_t calHi;   // highest gauge displayed value
};

calVal cal[13] = {          // used to map sensor raw values to real units
  {0,1023,0,10},  // i_fuel  A0  uncal'd
  {0,1023,0,10},  // i_comp  A1  uncal'd
  {0,1023,0,10},  // i_fan1  A2  uncal'd
  {0,1023,0,10},  // i_fan2  A3  uncal'd
  {493,   133,   60, 290},  // A4-oil_t, cal'd Dec 19, 2024 
  {483,   150,   60, 290},  // A5-cool_t, R1 & R3 330Ω , 5600-56Ω, -2 - 212F, a/d 970-552 - calculated - (13334 measured cold - connected?)
                            // VDO coolant sensor 325-001 marked - VDO germany - D - 6-24 V - max 120C - 801/2/1 - 6 97
  {102,   308,   0, 30},    // A6-fuel_l, CAL-e-e 12/24, R1 & R3 330Ω, 41-250Ω E-F, 0-30 gal, a/d 542-653 - calculated CAL'D should be good - (13338 measured full - connected?)
  {7760,  23600, 0, 7},     // A7-evap_p, PN# 09430128 BX22298 Holds @ 10 in. HO2  0psi=1.457V 7760,  6.5 4.53v" 23600  cal'd E-E
                            // {7080,  24140, 0, 15},    // 7-evap_p, PN# 12209219 4125A Holds @ 10 in. HO2  0psi=1.37V 7330,  7" 4.60v" 23660  cal'd e-e
  {90,    890,   0, 80},    // A8-fuel_p,  0psi 2240,  80psi=22550 4.29v @ 80psi-sensor  CAL'D end-end
                            // {2240,  22550, 0, 80},   // 6-fuel_p, 0psi 0.6v 2440, 100psi=3.59v 15950, (100-psi sensor  CAL'D end-end 12/2024)
  {2700,  23865, 0, 150},   // A9-ac_hp - (0-400psi min - not connected)
  {2650,  24220, 0, 100},   // A10-oil_p. oil_p = (((oil_p2 / 204.6) * 32) - 16) - (65526 measured idle - connected?)
                            // {2630,  25165, 0, 100},   // 10-oil_p1 = (((oil_p1 / 204.6) * 32) - 16);  E-ROD
  {296,   840,   0, 100},   // A11-thr, 0.5 – 4.5 volt signal ranging from 0 – 100 % - CAL'D
  {296,   840,   0, 100},   // A12-MAP
};

int      fake_raw[15]   = {0,0,0,0,0,  0,0,0,0,0, 0,0,0,0,0};
int      curr_val[15]   = {0,0,0,0,0,  0,0,0,0,0, 0,0,0,0,0};   // integer equivalent  -- Should this be type int? ---------------?
int      last_val[15]   = {0,0,0,0,0,  0,0,0,0,0, 0,0,0,0,0};   // prior displayed point used to smooth movement of pointer to next location
float    damping[15]    = {.2,0,0,0,0, 0,0,0,0,0, 0,0,0,0,0};   // Dampening factor set max change allowed per update (20% = 0.2)
uint16_t refresh[15]    = {0,0,0,0,500,  0,0,0,0,0, 0,0,0,0,0}; // milliseconds between updates
uint16_t timeTarget[15] = {0,0,0,0,0,  0,0,0,0,0, 0,0,0,0,0};   // Rolling target for next refresh


struct settings { 
  int valLT;    // Historical Low
  int valHT;    // Historical High

  int start;    // lowest value shown on scale 
  int crit_l;   // critical alarm point for input - triggers master warning flag
  int warn_l;   // warning value to draw attention - will set gauge color change with upcoming update
  int norm_l;   // start of normal running range
  
  int norm_h;   // end of normal running range
  int warn_h;   // high side warning
  int crit_h;   // High alarm point
  int stop;     // highest displayed scale point
};
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

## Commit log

2024-12-14 Initial post of Schematic and Code to Git
    [DIY_Engine_monitoring-06.csv, DIY_Engine_monitoring-06.kicad_pcb, DIY_Engine_monitoring-06.kicad_sch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]
2024-12-19 Updates include photos, harness drawings and code
    Early prototype partally working. Photos of Earlier version undergoing testing. PCB files are for next version.
    [DIY_Engine_monitoring-06.kicad_sch, Harness_DIY_Engine_monitoring-06.kicad_pcb, Harness_DIY_Engine_monitoring-06.kicad_sch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]
2024-12-21 Many calibrations made
    Still early days of getting code fixes and analog inputs calibrated
    [DIY_Engine_monitoring-06.kicad_sch, Harness_DIY_Engine_monitoring-06.kicad_pcb, Harness_DIY_Engine_monitoring-06.kicad_sch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]
